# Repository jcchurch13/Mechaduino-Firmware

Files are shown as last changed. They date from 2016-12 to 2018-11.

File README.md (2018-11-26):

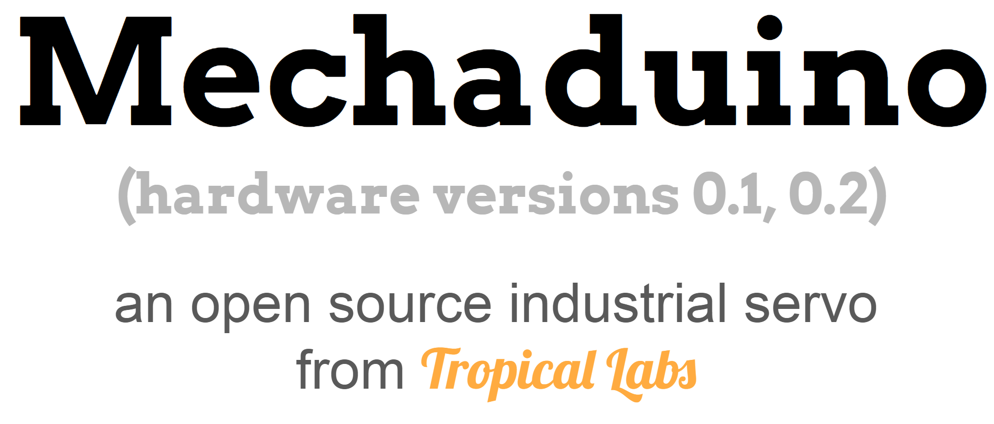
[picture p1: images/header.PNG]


New release 11/26/2018!  The calibration table is now stored in flash memory!  (Many thanks to osresearch!) We've also fixed a couple of small bugs.
Here are some preliminary instructions on how to get your Mechaduino up and running.  For more details, see the Mechaduino Manual above!



## Bootloader:
You will need to make sure your Mechaduino has the latest Arduino Zero bootloader.  If you got your Mechaduino from Tropical Labs, it will already have this! Otherwise you will need an Atmel-ICE or similar SWD programmer...

## Firmware:

Compile the Mechaduino firmware in the Arduino IDE and upload to your Mechaduino.  (Mechaduino will appear as an Arduino Zero.)  

New firmware is in the default "master" branch. Older versions are available [here](https://github.com/jcchurch13/Mechaduino-Firmware/releases). 

## Calibration Routine:

The first thing you will need to do is run the encoder calibration routine.

With the Mechaduino connected to your computer, open a serial monitor (115200 baud) in the Arduino IDE.  You will need to provide V+ to the Mechaduino to power the motor drivers (needed to calibrate).  A menu should appear explaining the basic commands (you can call the menu up at any time by typing 'm').  Type "s" and press enter a couple times to verify that everything is working.  The Mechaduino should step like a stepper.  It is currently in open loop mode.  press "d" and the stepping direction will change.  

Now, make sure nothing will touch the Mechaduino’s shaft during the calibration routine. If possible, completely disconnect any load that is attached to the Mechaduino’s shaft.  Type "c" to start the calibration routine. The Mechaduino will now step through all full steps to calibrate the encoder. In the latest version of the firmware, the calibration table will automatically be stored in non-volatile flash memory. When this routine is complete, your Mechaduino is now calibrated!

## Basic Commands:

As long as you have "serialCheck();" in your main loop, you can use the following built in commands to control the mechaduino from a serial monitor:

s - step (steps one full step in open loop mode)

d - dir (changes step direction in open loop mode)

p - print angle [step count] , [assumed angle] , [encoder reading]

c - calibration routine

e - check encoder diagnostics

q - parameter query (prints current PID values and cal table)

x  -  position mode

v - velocity mode

t - torque mode

y - enable control loop (enter closed loop mode)

n - disable control loop (go back to open loop mode)

r - enter new setpoint (new setpoint for control loop)

j - step response

k - edit controller gains*

g - generate sine commutation table

m - print main menu

  ...see serialCheck() in Utils for more details

##License

All Mechaduino related materials are released under the
[Creative Commons Attribution Share-Alike 4.0 License](https://creativecommons.org/licenses/by-sa/4.0/)

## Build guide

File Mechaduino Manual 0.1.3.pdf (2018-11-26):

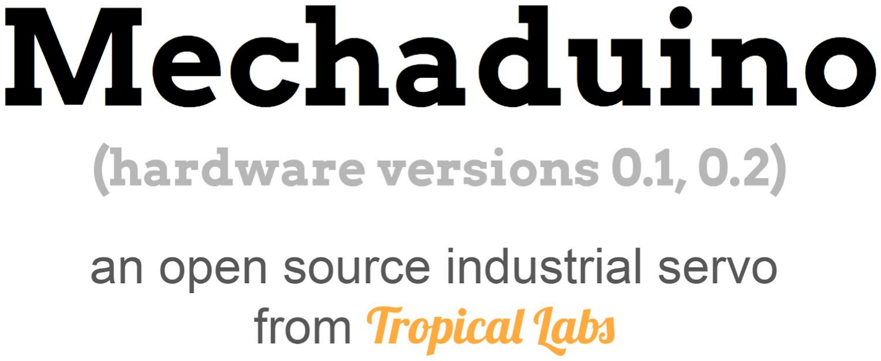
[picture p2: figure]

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
al v

0.1.3

# Table of Contents

Table of Contents | 2
Introduction | 4
Updates | 5
Overview of Specifications | 6
Microcontroller: SAMD21G18A | 6
Encoder: AS5047D or AS5048A | 6
Motor Driver: A4954 | 6
Motor included with Mechaduino Servo: 17HS16-2004S1 | 6
Magnet: Diametrically Magnetized NdFeBr | 7
Mounting Hardware: | 7
Getting Started | 8
Assembly: | 8
Firmware: | 9
Calibration Routine: | 10
Basic Commands: | 11
First Moves: | 12
Troubleshooting | 13
Tune Control Loop: | 14
Hardware: | 15
Board Versions: | 15
Board Layout | 16
Pin Diagram | 17
Power Connections | 18
Step/Dir Wiring Diagram | 19
Firmware v0.1.5 | 20
Overview | 20
Files | 20
Block Diagram | 21
Variables | 21
Control Algorithms: | 22
Position Mode: | 22

Mechaduino Manual v0.1.3

Velocity Mode: | 23
Torque Mode: | 23
Functions | 24
Examples | 25
Serial Interface | 25
Step/Dir Interface | 26
Button | 28
Print | 29
Torque Detect | 30
Slow Moves | 31
License | 33

# Introduction

Mechaduino is an Arduino for mechatronics! Mechaduino is a self-contained motion control platform which allows you to develop your own custom servo mechanisms. It can be also be used as a drop-in servo motor for 3D printers and CNC machines. No more missed steps!

# Updates

There are a few updates to the Mechaduino firmware in version v0.1.5:

- Calibration routine is now automatically stored in nonvolatile flash memory!
- Setpoint is set to current position when closed loop is enabled.
- Phase currents are set to zero (off) when closed loop is disabled.

In this version of the Mechaduino Manual, we’ve added documentation for the new calibration routine. We’ve also added in some notes and clarifications to address frequently asked questions.

# Overview of Specifications

Microcontroller: SAMD21G18A (http://www.atmel.com/Images/Atmel-42181-SAM-D21_Datasheet.pdf)

ARM Cortex-M0+ CPU running at 48MHz
Arduino Zero (https://www.arduino.cc/en/Main/ArduinoBoardZero) compatible
Operating Voltage: 3.3V
NOTE: only pins D0 and D1 have level converters for use with 5V logic. All others are 3.3V
Encoder: | AS5047D (http://www.mouser.com/ds/2/588/AS5047D_DS000394_2-00-347336.pdf) or AS5048A (https://www.mouser.com/datasheet/2/588/AS5048_DS000298_4-00-1100510.pdf)

^ (March-June 2018 - see note)
Resolution: | 14bit
Accuracy: | about ±0.1° worst case after calibration routine*
Interface: | SPI
Motor Driver: | A4954 (http://www.allegromicro.com/~/media/Files/Datasheets/A4954-Datasheet.ashx)

Dual Full-Bridge DMOS PWM Motor Driver
Peak output currents: ±2 A

Motor included with Mechaduino Servo: 17HS16-2004S1 (https://www.omc-stepperonline.com/hybrid-stepper-motor/nema-17-bipolar-45ncm-64ozin-2a-42x40mm-4wires-w-1m-cable-and-connector-17hs16-2004s1.html)

Motor Type: | Bipolar Stepper
Step angle: | 1.8°
Holding Torque: | 45Ncm (63.7oz.in)
Rated Current/phase: | 2A
Phases: | 2
Positional accuracy: | ±5%
Phase Resistance: | 1.1ohms
Inductance: | 2.6mH±20%(1KHz)
Rotor Inertia | 54gcm²
Frame Size: | NEMA 17 (42mm X42mm)

*This is limited by the positional accuracy of the stepper motor that you use. This encoder has an integral nonlinearity of up to ±0.8°. Our calibration routine uses the stepper motor’s full step positions as references to calibrate out most of this error. Most stepper motors claim a full step accuracy of ±5% or better.

Magnet: Diametrically Magnetized NdFeBr (http://www.kjmagnetics.com/proddetail.asp?prod=D42DIA)

Mount about 1mm-2mm from encoder chip. Use epoxy/superglue to secure to shaft. Calibration routine corrects for minor misalignment.

## Mounting Hardware:

We use m3 threaded rods epoxied into 4mm M3 standoffs. Be careful not to remove all motor screws at once while installing: Opening a stepper motor can weaken its magnetization.

# Getting Started

### Assembly:

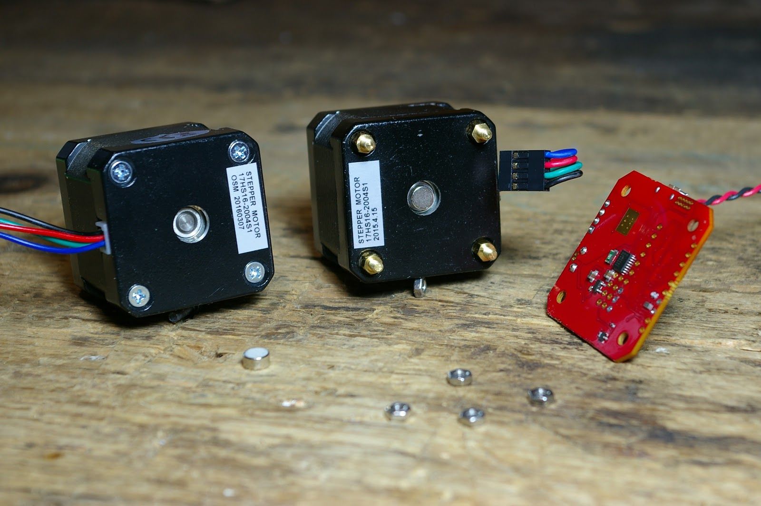
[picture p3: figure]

You will need to mount the magnet to the back of the motor shaft. Note: the magnet must be diametrically magnetized, as opposed to axially magnetized. The magnet may naturally stick to the shaft, but we recommend a dab of epoxy or super glue to hold it in place. The magnet should be fairly centered, but the calibration routine will correct for minor misalignment.

The Mechaduino PCB must be mounted so that the magnet is directly under the encoder chip. (Close but not touching. About 1-2mm. See the AS5047/AS5048 datasheet for details.) We replaced the standard motor hardware with M3 threaded rods and short standoffs to mount on our assembled Mechaduino Servos, but there are other ways this could be done.

When wiring your motor up to the Mechaduino board, please make sure that one phase is connected to outputs 1&2, and the other phase is connected to outputs 3&4.

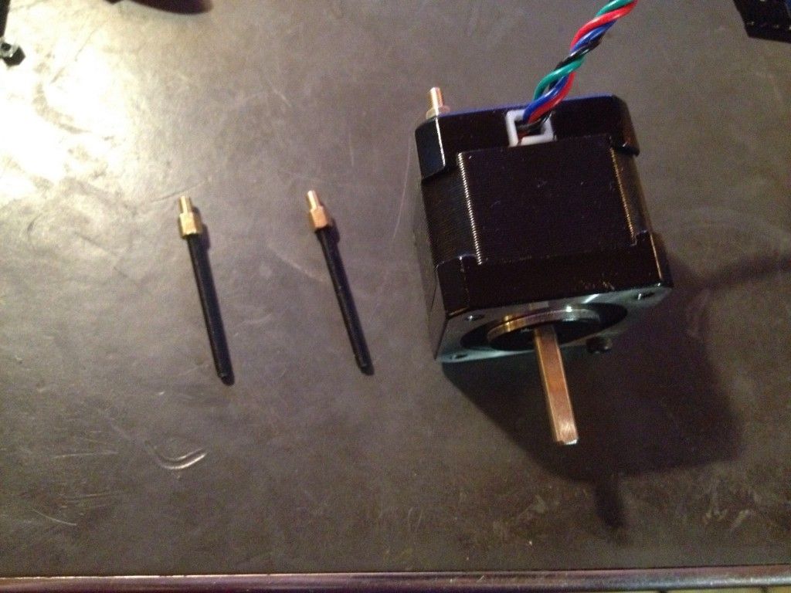
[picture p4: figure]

## Firmware:

Next, you need to install the firmware:

The Mechaduino firmware can be compiled/edited/uploaded using the popular Arduino IDE:

https://www.arduino.cc/en/Main/Software

Once you have the Arduino IDE installed, you will need to add Arduino Zero support. Open the Arduino IDE, navigate to Tools>Board:...>Board Manager and install the latest "Arduino SAMD (32-bits ARM Cortex-M0+)" .

Now go to Tools>Board and select “Arduino/Genuino Zero (Native USB Port)”.

At this point you can connect your Mechaduino via USB. It will appear as an Arduino Zero. (If it does not appear, please make sure any drivers have finished installing, then try hitting the reset button or disconnecting/reconnecting the hardware. Double clicking the reset button puts the arduino zero into a “bootloader mode” which may make it easier to connect to.)

Download the latest Mechaduino firmware (https://github.com/jcchurch13/Mechaduino-Firmware) (the ‘master’ branch on GitHub), open it in the Arduino IDE, compile it, and upload to your Mechaduino. Previous versions of the firmware are available here. (https://github.com/jcchurch13/Mechaduino-Firmware/releases)

### 1.8 vs 0.9 degree steppers:

By default the firmware assumes a 1.8 degree (200 steps per rev) stepper. If you are using a 0.9 degree (400 steps per rev) or other size stepper, you will need to adjust the parameter “spr” (steps per rev) in parameters.cpp.

const int spr = 200; // 200 steps per revolution -- for 400 step/rev, you only need to edit this value

## Calibration Routine:

Once you have the firmware installed, you will need to run the encoder calibration routine.

With the Mechaduino connected to your computer, open a serial monitor (115200 baud) in the Arduino IDE. You will need to provide V+ to the Mechaduino to power the motor drivers (needed to calibrate). Type "s" and press enter a couple times to verify that everything is working. The Mechaduino should step like a stepper. It is currently in open loop mode. press "d" and the stepping direction will change.

Now, make sure nothing will touch the Mechaduino’s shaft during the calibration routine. If possible, completely disconnect any load that is attached to the Mechaduino’s shaft. Type "c" to start the calibration routine. The Mechaduino will now step through all full steps to calibrate the encoder. In the latest version of the firmware, the calibration table will automatically be stored in non-volatile flash memory. When this routine is complete, your Mechaduino is now calibrated!

Please note that the calibration table will be overwritten if you re-upload the firmware. While it is no longer necessary to copy a lookup table into the firmware to complete the calibration, you may want to do so in order to avoid having to recalibrate. You can print the calibration table to the serial monitor by pressing “q”. A very long lookup table (16,384 entries) will be printed to the serial monitor. These are the calibrated angles at each encoder count. You can copy these into the Parameters.cpp file here:

//This is the encoder lookup table (created by calibration routine):

const float __attribute__((__aligned__(256))) lookup[16384] = { //Put lookup table here!
};

You can easily select the whole lookup table from the serial monitor by clicking on the next line and dragging the cursor up.
Save, compile, and re-upload the firmware to your Mechaduino. Your Mechaduino is now ready to use without re-calibrating. Please note that you will need to generate a new calibration table for each Mechaduino.

## Basic Commands:

As long as you have "serialCheck();" in your main loop, you can use the following built in commands to control the Mechaduino from a serial monitor:

Implemented serial commands are:

s - step | (steps one full step in open loop mode)
d - dir | (changes step direction in open loop mode)
p - print angle [step count] , [assumed angle] , [encoder reading]

c - calibration routine
e - check encoder diagnostics (does not work in closed loop mode)
q - parameter query | (prints current PID values and cal table)
x - position mode | (set mode for closed loop operation)
v - velocity mode
t - torque mode
y - enable control loop | (enter closed loop mode)
n - disable control loop | (go back to open loop mode)
r - enter new setpoint | (new setpoint for control loop)

j - step response
k - edit controller gains*
g - generate sine commutation table m - print main menu

See serialCheck() in Utils for more details

*Note, these edits are stored in volatile memory and will be reset if power is cycled

## First Moves:

Once you’ve calibrated the Mechaduino, try out the closed loop position mode:

1. Type “x” and then enter into the serial monitor to set position mode.
2. Type “y” then enter to enable closed loop mode.
3. Type “r” and then enter to change the setpoint. You will be prompted to enter a setpoint angle.
4. Try entering various setpoint to see how the mechaduino moves. For example, try 0 to find where zero is, and then try 720 to see the Mechaduino do two full rotations. Try 0 and then 0.5 to see the Mechaduino move half of a degree.
5. Try moving the Mechaduino’s shaft with your hand. Watch to make sure it returns to the desired setpoint.
6. Disable closed loop mode by typing “n” and then enter.

Set the setpoint back to zero, and then try out velocity and torque modes in the same way as above. (Make sure the setpoint is zero before changing modes to avoid rapid movements!)

## Troubleshooting:

If you are having trouble connecting and uploading to the Mechaduino, please try the following:

- Make sure you have “Arduino/Genuino Zero (Native USB Port)” selected under Tools>Board in the Arduino IDE.
- Try clicking/double clicking the reset button on the Mechaduino.

If neither of those work, please check to make sure that the Mechaduino is appearing as a COM port under Tools>Com. The port number may change if you disconnect the Mechaduino, hit reset, or upload firmware. If it does not appear at all, there may be an issue with your hardware.

If closed loop mode does not behave as expected:

- First, try running in closed loop mode without a mechanical load, using the default controller parameters. Depending on the load, you may need to tune the controller.
- Make sure your lookup table looks reasonable. You can view the lookup table by pressing ‘q’ in the serial monitor. You should see ascending values that increment by approximately 0.02 per entry, wrapping around to zero once they reach 360.
- If the lookup table does not look right, make sure the magnet is placed close enough to the encoder on the Mechaduino. Try the ‘e’ command to view the encoder diagnostics (do this in open loop mode. Readings may be erratic in closed loop mode).

## Tune Control Loop:

At this point you may need to tune the controller gains. By default, the position and velocity loops have PID controllers with parameters that can be edited in Parameters.cpp:

//----Current Parameters-----

volatile float Fs = 6500.0; | //Sample frequency in Hz
volatile float pKp = 10.0; | //position mode PID values.
volatile float pKi = 0.15;
volatile float pKd = 20.0;
volatile float vKp = 0.05; | //velocity mode PID values.
volatile float vKi = 0.033;
volatile float vKd = 3.0;

To tune the control loop from the serial monitor:
- Connect your Mechaduino to your computer and open up a serial monitor
- Use the commands ‘x’ followed by ‘y’ to enter closed loop position mode
- Use the command ‘k’ to bring up the tuning menu
- Adjust the parameters until you get a good response
- To make these changes permanent, you will need to copy these values into the Parameters.cpp file and re-upload.
- You can compare tunings by using the step response command ‘j’. (You must exit the tuning menu first.)

PID values will vary a lot depending on the motor you use and the load you have connected to your motor. There are lots of resources online that discuss PID tuning, but here are some simple pointers:
-Start with a low proportional gain and no integral or derivative action. If the motor seems to buzz or behave erratically, then your Kp is probably too high. Try setting Kp low enough that the motor behaves like a fairly compliant spring about the setpoint.
-Slowly increase Kp to improve the stiffness of the control. Adding integral action can remove steady state errors. Derivative action can also be added in to improve performance.

# Hardware:

## Board Versions:

The Mechaduino 0.2 hardware is backwards compatible with the Mechaduino 0.1 and features the following improvements:

- Four 5V level-shifted digital I/O (D0, D1, D2, & D3)
- Better thermal design for A4954 driver
- Higher voltage capacitors allow for a max V+ of 35V
- Small vias provided to break out encoder A/B/I interface and rsense voltages (for experimental use)
- No more traces under mounting screws*
- No traces under AS5047 encoder
- Simplified power circuit

Note: Mechaduinos purchased between 3/1/2018 amd 7/1/2018 used an AS5048A encoder instead of the AS5047D (due to supply availability). As far as the Mechaduino is concerned, the two parts are virtually identical. However, we just became aware that the as5048a's error register has a slightly different address. To correct this issue, you can change lines 610 and 611 in Utils.cpp to the following:

SPI.transfer(0x7F);
SPI.transfer(0xFD);

*Bottom solder mask under OSHW logo can be scraped away to provide single ground point to motor.

## Board Layout

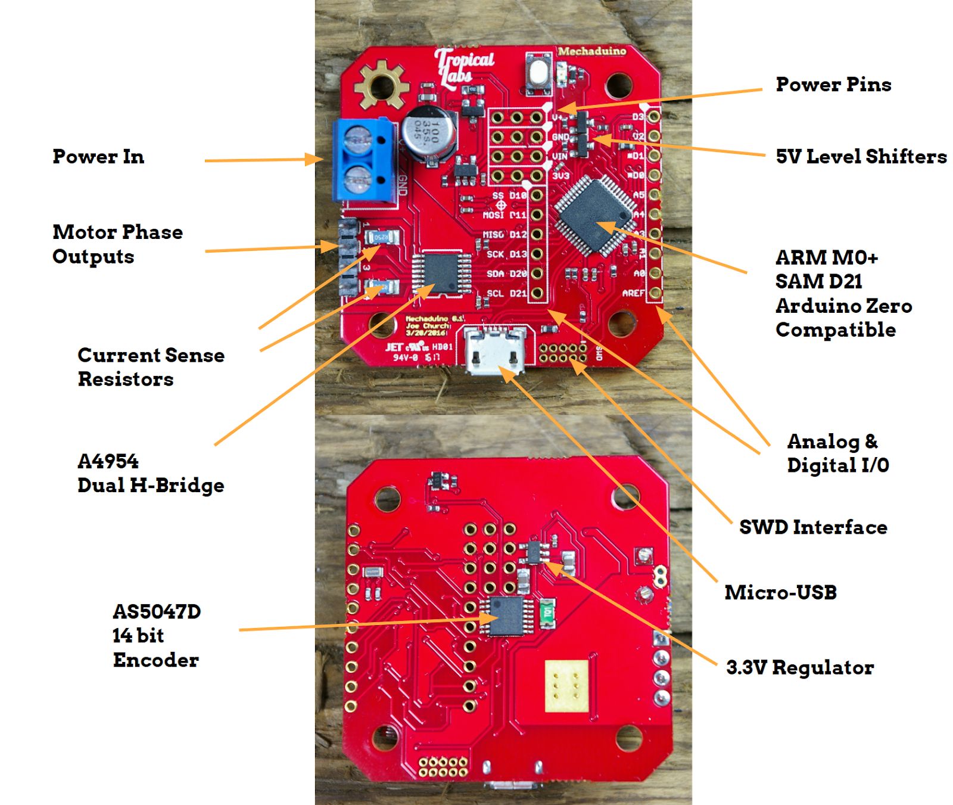
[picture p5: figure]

Version 0.1 shown, version 0.2 is very similar.

## Pin Diagram

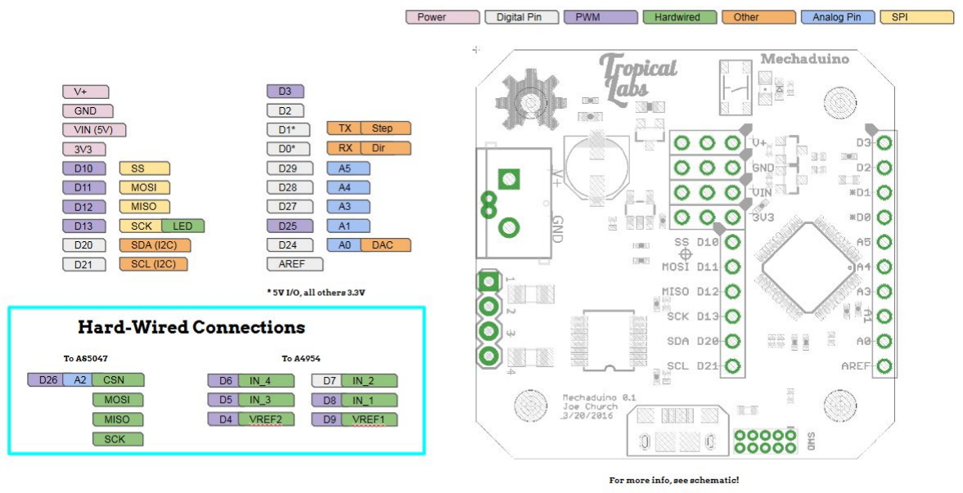
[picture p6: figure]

Version 0.1 shown, version 0.2 has four 5V I/O : D0,D1,D2,& D3.

## Power Connections

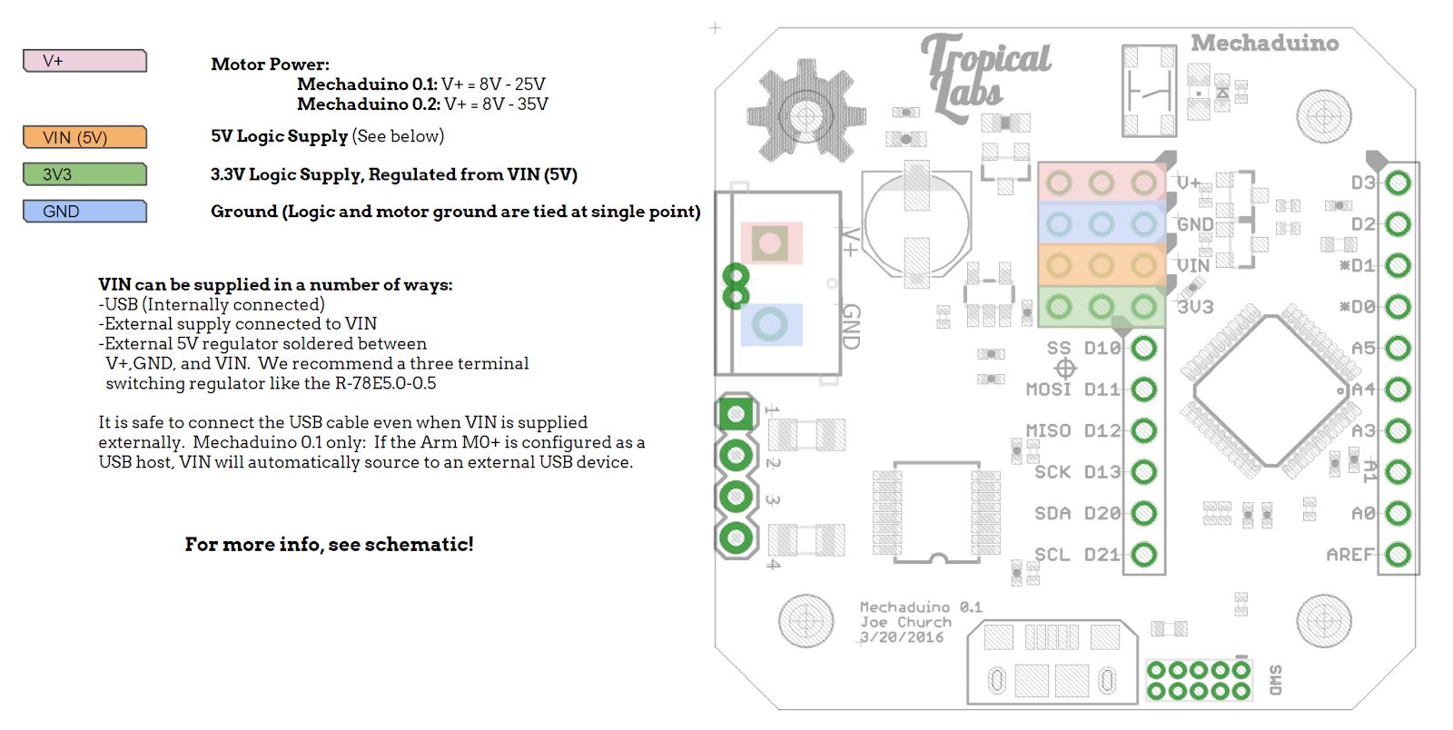
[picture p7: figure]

## Step/Dir Wiring Diagram

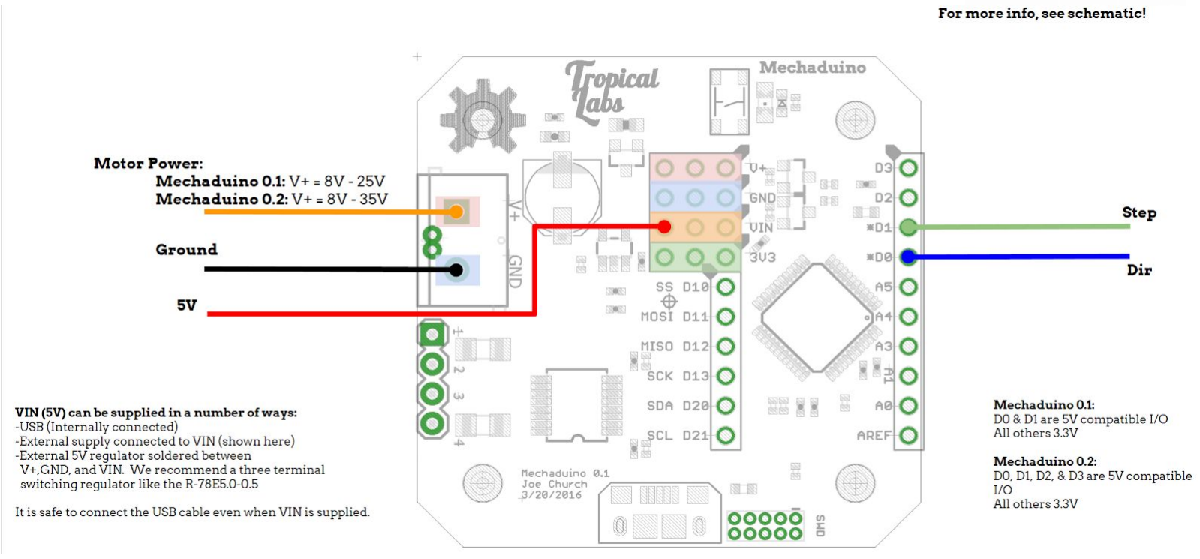
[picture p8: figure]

# Firmware v0.1.5

## Overview

The Mechaduino Firmware can be edited, compiled and uploaded from the popular Arduino IDE. It is written in Arduino language (https://www.arduino.cc/en/Reference/HomePage) (similar to C/C++). You can script the Mechaduino’s behavior in the main loop of the file Mechaduino_01.ino. The stock Mechaduino firmware is configured to listen for serial commands using serialCheck(). A step/dir interrupt can be enabled to increment/decrement the setpoint variable.

## Files

Mechaduino_01.ino
This is the main file that contains setup(), (https://www.arduino.cc/en/Reference/Setup) which runs once on startup and loop() (https://www.arduino.cc/en/Reference/Loop) which runs thereafter.

Controller.cpp
Contains the TC5_Handler() which executes at 6.5kHz* when enabled and contains the closed loop control algorithms. For more info on configuring TC5, please see this. (http://www.atmel.com/Images/Atmel-42181-SAM-D21_Datasheet.pdf#page=635)

Parameters.cpp
Contains configurable parameters including PID gains, calibration table, and other constants.

State.cpp
Contains controller state variables.

Utils.cpp
Contains utility function definitions.

AnalogFastWrite.c
The latest arduino zero board files (1.6.7 and up) have a much lower PWM frequency than previous versions (732.4Hz , down from 187.5kHz). This causes audible hissing when used with the Mechaduino. We added the
analogFastWrite command to provide 187.5kHz PWM to eliminate this issue.

Additionally, the header files (.h) contain function declarations and macro definitions for the above files. Utils.h is a good reference since it gives a list of all the implemented utility functions.

*Set by Fs in Parameters.cpp which changes TC5->COUNT16.CC[0].reg = (int)( round(48000000 / Fs)); in setupTCInterrupts() in Utils.cpp.

## Block Diagram

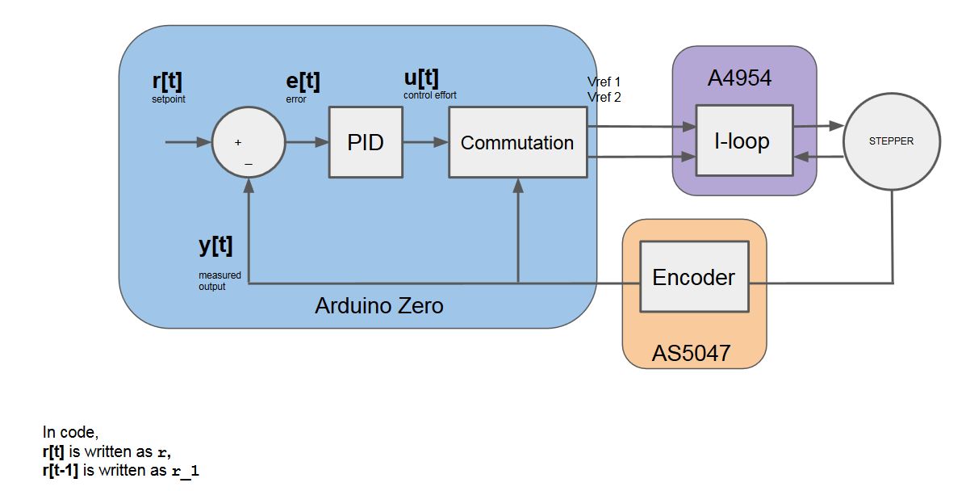
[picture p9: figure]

## Variables

Important global variables include controller state variables and configuration parameters. While the use of global variables is sometimes frowned upon, we wanted these values to be accessible and modifiable to make it easier to develop custom applications (see the example section of this document). Similarly, we chose to use floating point math for the controller instead of fixed point math. While fixed point math would be faster, we’ve found that our floating point algorithms are generally fast enough, and are much more readable. As a result, many of these variables are floats. Here is an overview:

Name | Description | Type | range | unit | Definition Location
r | Control loop setpoint | float | N/A | Degrees in position mode…. | State.cpp
y | Corrected encoder reading | float | 0.0 to 360.0 | degrees | State.cpp
yw | Wrapped angle (keeps track of revolutions) | float | N/A | degrees | State.cpp
e | Error (r-yw) | float | N/A | degrees | State.cpp
u | Control effort | float | -uMAX to uMAX | Bits ( 8.6mA/bit)* | State.cpp

*(3.3V/255bits)*(1A/10*rsense)= 8.6mA

## Control Algorithms:

## Position Mode:

The default position mode controller is a PID controller of the following form (represented as discrete transfer functions (https://en.wikipedia.org/wiki/Transfer_function) using the z-transform): (https://en.wikipedia.org/wiki/Z-transform)

u(z) = Pterm(z) + Iterm(z) + Dterm(z)

e = r − yw

(z) pKp e

Pterm =

(z)
e

Iterm = z − 1

pKi z

(z) − Kd 1 )
yw
Dterm | = p | * ( − a (z−a) (z−1)

In code, this is implemented with the following difference equations:

e = (r - yw);

ITerm += (pKi * e); | //Integral wind up limit
if (ITerm > 150.0) ITerm = 150.0;
else if (ITerm < -150.0) ITerm = -150.0;

DTerm = pLPFa*DTerm - pLPFb*pKd*(yw-yw_1);

u = (pKp * e) + ITerm + DTerm;

A couple notes:

-Dterm is calculated from angle measurement, yw, rather than from error. This is a common practice that prevents jumps from step reference commands, but provides the same damping. (This is why there is a negative sign: e = r - y)

-Dterm has a first order low pass filter. The breakpoint of the filter is set by adjusting pLPF (in hertz) and is calculated as follows:

a = e

(sTs) = e

(−pLPF*2pi*Ts)
(in code, a is pLPFa)

## Velocity Mode:

The default velocity mode controller is a PID controller of the following form (represented as discrete transfer functions (https://en.wikipedia.org/wiki/Transfer_function) using the z-transform): (https://en.wikipedia.org/wiki/Z-transform)

u(z) = Pterm(z) + Iterm(z) + Dterm(z)

− 1 | ) Fs | 0.16666667

v

yw = ( − a * | * | * (z−a) (z−1)

e = (r − v);

(z) pKp e

Pterm =

(z)
e

Iterm = z − 1 pKi z

(z) Kd e
Dterm | = p | * (z) (z−1)

In code, this is implemented with the following difference equations:

v = -(vLPFa*v + vLPFb*(yw-yw_1)); | //filtered velocity
e = (r + v); | //error in degrees per rpm (sample frequency in Hz*(60 seconds/min)/(360 degrees/rev))
ITerm += (vKi * e); | //Integral wind up limit
if (ITerm > 200) ITerm = 200;
else if (ITerm < -200) ITerm = -200;

u = ((vKp * e) + ITerm - (vKd * (e-e_1)));

A couple notes:

v, the filtered, measured velocity, has a first order low pass filter. The breakpoint of the filter is set by adjusting pLPF (in hertz) and is calculated as follows:

a = e

(sTs) = e

(−pLPF*2pi*Ts)
(in code, a is vLPFa)

## Torque Mode:

In torque mode, the setpoint r directly sets the control effort u, which in turn sets the current level. The a4954 driver chip has an internal current loop that forces the motor phase current to the commanded level. The torque exerted by the Mechaduino is equal to the motor torque constant times the phase current.

## Functions

void setupPins(); | // initializes pins
void setupSPI(); | // initializes SPI
void configureStepDir(); | // configure step/dir interface
void configureEnablePin(); | // configure enable pin
void stepInterrupt(); | // step interrupt handler
void dirInterrupt(); | // dir interrupt handler
void enableInterrupt(); | // enable pin interrupt handler
void output(float theta, int effort); | // calculates phase currents (commutation) and outputs to Vref pins
void calibrate(); | // calibration routine
void serialCheck(); | // checks serial port for commands. Must include this in loop() for serial interface to work
void parameterQuery(); | // prints current parameters
void oneStep(void); | // take one step
int readEncoder(); | // read raw encoder position
void readEncoderDiagnostics(); | // check encoder diagnostics registers
void print_angle(); | // for debugging purposes in open loop mode: prints [step number] , [encoder reading]
void receiveEvent(int howMany); | // for i2c interface...
int mod(int xMod, int mMod); | // modulo, handles negative values properly
void setupTCInterrupts(); | // configures control loop interrupt
void enableTCInterrupts(); | // enables control loop interrupt. Use this to enable "closed-loop" modes
void disableTCInterrupts(); | // disables control loop interrupt. Use this to disable "closed-loop" mode
void antiCoggingCal(); | // under development...
void parameterEditmain(); | // parameter editing menu
void parameterEditp(); | // parameter editing menu
void parameterEditv(); | // parameter editing menu
void parameterEdito(); | // parameter editing menu
void hybridControl(); | // open loop stepping, but corrects for missed steps. under development
void serialMenu(); | // main menu
void sineGen(); | // generates sinusoidal commutation table. you can experiment with other commutation profiles
void stepResponse(); | // generates position mode step response in Serial Plotter
void moveRel(float pos_final,int vel_max, int accel); | // Generates trapezoidal motion profile for closed loop position mode
void moveAbs(float pos_final,int vel_max, int accel); | // Generates trapezoidal motion profile for closed loop position mode

# Examples

Below are a few examples. Please note that there are a few changes from previous versions of the firmware (specifically for the step/dir interface).

## Serial Interface

As long as the function serialCheck() is included in your loop (it is by default), you can use the built in serial commands. (Full list here.) You can also create your own by creating a function and adding it to serialCheck().

The serial interface is useful for debugging/initial testing. Generally, when using a Mechaduino in a new application, we might do the following:

- Connect to computer, open serial monitor
- Run cal routine, copy table to firmware, recompile, and upload
- Connect Mechaduino to mechanical load
- Set closed loop position mode using commands ‘x’, ‘y’
- Tune PID loop using ‘k’ (parameter edit) and ‘j’ (step response) commands
- Copy best PID values to firmware, recompile, and upload
- Move Mechaduino to various setpoints in closed loop mode using ‘r’ command to test out application

## Step/Dir Interface

Here is how to correctly enable the step/dir interface for use with a 3D printer/CNC machine after calibrating and tuning your PID loop.

void setup() | // This code runs once at startup
{
digitalWrite(ledPin,HIGH); | // turn LED on
setupPins(); | // configure pins
setupTCInterrupts(); | // configure controller interrupt

SerialUSB.begin(115200);
delay(3000); | // This delay seems to make it easier to establish a connection when the
Mechaduino is configured to start in closed loop mode.
serialMenu(); | // Prints menu to serial monitor
setupSPI(); | // Sets up SPI for communicating with encoder
digitalWrite(ledPin,LOW); | // turn LED off

// Uncomment the below lines as needed for your application.
// Leave commented for initial calibration and tuning.
| configureStepDir(); | // Configures setpoint to be controlled by step/dir interface
// | configureEnablePin(); | // Active low, for use wath RAMPS 1.4 or similar
| enableTCInterrupts(); | // uncomment this line to start in closed loop
| mode = 'x'; | // start in position mode
}

////////////////////////////////////// /////////////////LOOP///////////////// //////////////////////////////////////

void loop() | // main loop
{
serialCheck(); | //must have this execute in loop for serial commands to function
//r=0.1125*step_count; | //Don't use this anymore, step interrupts enabled above by //"configureStepDir()", adjust step size in parameters.cpp

}

You can adjust the step size by changing the stepangle variable in Parameters.cpp:

const int spr = 200; // 200 steps per revolution -- for 400 step/rev, you only need to edit this value
const float aps = 360.0/ spr; | // angle per step
int cpr = 16384; | // counts per rev
const float stepangle = aps/32.0; | // for step/dir interrupt: aps/32 is the equivalent of 1/32 microsteps

By default the stepangle is set to the equivalent of 1/32 microstepping.

If you would like to use an enable pin, you can uncomment this line:

configureEnablePin(); | // Active low, for use wath RAMPS 1.4 or similar

Note that only pins D0 & D1 have built in level converters. You will need to step down a 5V enable signal to 3.3V. You could use a level converter board like this, (https://www.sparkfun.com/products/12009) or a simple resistor divider.

## Button

In this code, when digital pin 3 goes HIGH, the Mechaduino moves from 0 to 90 degrees, holds that position for 3 seconds, and then goes back.

void setup() | // This code runs once at startup
{
digitalWrite(ledPin,HIGH); | // turn LED on
setupPins(); | // configure pins
setupTCInterrupts(); | // configure controller interrupt

SerialUSB.begin(115200);
delay(3000); | // This delay seems to make it easier to establish a connection when the
Mechaduino is configured to start in closed loop mode.
serialMenu(); | // Prints menu to serial monitor
setupSPI(); | // Sets up SPI for communicating with encoder
digitalWrite(ledPin,LOW); | // turn LED off

// Uncomment the below lines as needed for your application.
// Leave commented for initial calibration and tuning.
// | configureStepDir(); | // Configures setpoint to be controlled by step/dir interface
// | configureEnablePin(); | // Active low, for use wath RAMPS 1.4 or similar
| enableTCInterrupts(); | // uncomment this line to start in closed loop
| mode = 'x'; | // start in position mode

pinMode(3, INPUT);
}

////////////////////////////////////// /////////////////LOOP///////////////// //////////////////////////////////////

void loop() | // main loop
{
r = 0;
if (digitalRead(3) == HIGH){
r = 90;
delay(3000);
}
}

## Print

Here is some demo code showing how to print some of the the state variables to the serial monitor while the Mechaduino is running. You can access these variables and use them in other ways as well. For example you could toggle some of the GPIO depending on the value of the position error e, or you could set an analog out pin proportional to the control effort u.

void setup() | // This code runs once at startup
{
digitalWrite(ledPin,HIGH); | // turn LED on
setupPins(); | // configure pins
setupTCInterrupts(); | // configure controller interrupt

SerialUSB.begin(115200);
delay(3000); | // This delay seems to make it easier to establish a connection when the
Mechaduino is configured to start in closed loop mode.
serialMenu(); | // Prints menu to serial monitor
setupSPI(); | // Sets up SPI for communicating with encoder
digitalWrite(ledPin,LOW); | // turn LED off

// Uncomment the below lines as needed for your application.
// Leave commented for initial calibration and tuning.
// | configureStepDir(); | // Configures setpoint to be controlled by step/dir interface
// | configureEnablePin(); | // Active low, for use wath RAMPS 1.4 or similar
| enableTCInterrupts(); | // uncomment this line to start in closed loop
| mode = 'x'; | // start in position mode

}

////////////////////////////////////// /////////////////LOOP///////////////// //////////////////////////////////////

void loop() | // main loop
{
serialCheck();

SerialUSB.print("setpoint: "); SerialUSB.print(r);
SerialUSB.print(", error: "); SerialUSB.println(e);
delay(100); //delay 0.1 seconds }

## Torque Detect

The Mechaduino can detect and react to external disturbances. In this example, exerting a slight torque in either direction on the Mechaduino’s rotor will cause the setpoint to advance in the corresponding direction by 90 degrees:

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

}

////////////////////////////////////// /////////////////LOOP///////////////// //////////////////////////////////////

void loop() | // main loop
{
if (u > 35){
r -= 90;
delay(100);
}
else if (u < -35){
r += 90;
delay(100);
}
}

The torque is detected by monitoring the control effort u in closed loop position mode.

## Slow Moves

By design, setting a setpoint in position mode causes the Mechaduino to snap to the new setpoint as fast as possible. This is not always ideal. There are a number of ways to create slow smooth motion in position mode.

One way is to use an external motion controller to create a trajectory of setpoints for the Mechaduino to follow. An example of this would be using the Mechaduino’s step/dir interface with a 3D printer or CNC machine. Here the motion profiles are generated in external firmware/software such as Marlin or Mach 3.

If you would like smooth motion in a stand-alone application, you can generate your motion profile on the Mechaduino itself. To illustrate this, here is a crude loop that will move the Mechaduinos setpoint from 0 to 90 degrees and back at constant speed:

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

SerialUSB.begin(115200);
delay(3000);
serialMenu(); | // Prints menu to serial monitor
setupSPI(); | // Sets up SPI for communicating with encoder
digitalWrite(ledPin,LOW); | // turn LED off

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

//////////////////////////////////////
/////////////////LOOP///////////////// //////////////////////////////////////
void loop() | // main loop
{

while (r < 90.0){
r += 0.1;
delayMicroseconds(100);
}
delay(2000);
while (r > 0.0){
r -= 0.1;
delayMicroseconds(100);
}
delay(2000);
}

We’ve gone a step further and implemented two commands that generate trapezoidal speed trajectories (constant acceleration, max speed, constant deceleration): moveRel() for relative movements; and moveAbs() for absolute movements. From Parameters.cpp:

void moveAbs(float pos_final,int vel_max, int accel){

//Use this function for slow absolute movements in closed loop position mode
//
// This function creates a "trapezoidal speed" trajectory (constant accel, and max speed, constant decel); // It works pretty well, but it may not be perfect
//
// pos_final is the desired position in degrees
// vel_max is the max velocity in degrees/second
// accel is the max accel in degrees/second^2
//
//Note that the actual max velocity is limited by the execution speed of all the math below. //Adjusting dpos (delta position, or step size) allows you to trade higher speeds for smoother motion //Max speed with dpos = 0.225 degrees is about 180 deg/sec
//Max speed with dpos = 0.45 degrees is about 360 deg/sec

And here’s an example showing how to use these functions:

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

SerialUSB.begin(115200);
delay(3000);
serialMenu(); | // Prints menu to serial monitor
setupSPI(); | // Sets up SPI for communicating with encoder
digitalWrite(ledPin,LOW); | // turn LED off

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

//////////////////////////////////////
/////////////////LOOP///////////////// //////////////////////////////////////
void loop() | // main loop
{
moveRel(360.0,100, 30);
delay(2000);
moveAbs(0.0,100,30);
delay(2000);
}

# License

All Mechaduino related materials are released under the Creative Commons Attribution Share-Alike 4.0 License (https://creativecommons.org/licenses/by-sa/4.0/)

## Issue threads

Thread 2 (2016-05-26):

Effective CPR count

iceblu3710, 2016-05-26:
From the code `int cpr = 16384; //counts per rev` seems quite an achievement with a hall effect encoder. What is the effective CPR that can be independently held and stepped to/from reliably?

jcchurch13, 2016-05-29:
Thanks for taking a look at our code!

CPR is our encoder "Counts Per Revolution": 2^14 or 16384.  Our closed loop position control actively forces the motor to move until the correct encoder position is reached.  This gives a resolution of 360 degrees/ 16384 = 0.02 degrees.  Thanks to our calibration routine, the accuracy should be close to the same (we're going to measure this soon).

We have measured repeatability by stepping into and out of full step positions in open loop mode 1000x and looking at the distribution of encoder readings. The results look promising:  I don't have the data in front of me, but the error distribution appeared to be Gaussian with zero mean, and a standard deviation of less than 1 LSB (0.02) degrees.  I'll post this data soon.

Thanks for your interest!  We're looking to get a really accurate, high resolution encoder for a test jig to measure the Mechaduinos accuracy at all encoder increments, not just one position.

Closed 2016-06-22.

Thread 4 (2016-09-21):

Debugging units: No movement in closed loop

SloMusti, 2016-09-21:
Self-built Mechaduino while waiting for Kickstarter units to arrive. Performed calibration routine and programmed it. Step mode with "s" command works. After sending "y" and "x" and "r 1080" no rotation occurs. Stepper axis can be easily moved my hand, there is some minor resistance, but no closed-loop control action occurs.

What parameters in the firmware to observe or print to evaluate what is going on.

jcchurch13, 2016-09-21:
Sounds like this may be an encoder issue.  Did the calibration routine yield a lookup table with numbers ascending by about 0.02?

SloMusti, 2016-09-22:
Please see the calibration values below, seems quite ok in the way the values are increasing. I have tried with different magnets and motors, but the problem persisted. I doubt the problem is in the H bridge or so as it works fine in the open loop step mode. But as soon as it gets into the closed loop mode, there is almost no torque on the axis.

`60.01 , 60.05 , 60.10 , 60.14 , 60.19 , 60.23 , 60.27 , 60.32 , 60.36 , 60.40 , 60.45 , 60.49 , 60.54 , 60.58 , 60.62 , 60.67 , 60.71 , 60.76 , 60.80 , 60.84 , 60.89 , 60.93 , 60.98 , 61.02 , 61.06 , 61.11 , 61.15 , 61.19 , 61.24 , 61.28 , 61.33 , 61.37 , 61.41 , 61.46 , 61.50 , 61.55 , 61.59 , 61.63 , 61.68 , 61.72 , 61.77 , 61.78 , 61.83 , 61.87 , 61.92 , 61.96 , 62.01 , 62.05 , 62.10 , 62.14 , 62.19 , 62.23 , 62.28 , 62.32 , 62.37 , 62.41 , 62.46 , 62.50 , 62.55 , 62.59 , 62.64 , 62.68 , 62.73 , 62.77 , 62.82 , 62.86 , 62.91 , 62.95 , 63.00 , 63.04 , 63.09 , 63.13 , 63.18 , 63.22 , 63.27 , 63.31 , 63.36 , 63.40 , 63.45 , 63.49 , 63.54 , 63.61 , 63.65 , 63.70 , 63.74 , 63.79 , 63.83 , 63.87 , 63.92 , 63.96 , 64.00 , 64.05 , 64.09 , 64.14 , 64.18 , 64.22 , 64.27 , 64.31 , 64.36 , 64.40 , 64.44 , 64.49 , 64.53 , 64.58 , 64.62 , 64.66 , 64.71 , 64.75 , 64.79 , 64.84 , 64.88 , 64.93 , 64.97 , 65.01 , 65.06 , 65.10 , 65.15 , 65.19 , 65.23 , 65.28 , 65.32 , 65.37 , 65.51 , 65.56 , 65.60 , 65.64 , 65.68 , 65.72 , 65.76 , 65.79 , 65.83 , 65.87 , 65.92 , 65.96 , 66.00 , 66.04 , 66.08 , 66.11 , 66.15 , 66.19 , 66.24 , 66.28 , 66.32 , 66.36 , 66.40 , 66.43 , 66.47 , 66.51 , 66.56 , 66.60 , 66.64 , 66.68 , 66.72 , 66.76 , 66.79 , 66.83 , 66.87 , 66.92 , 66.96 , 67.00 , 67.04 , 67.08 , 67.11 , 67.15 , 67.19 , 67.24 , 67.28 , 67.26 , 67.31 , 67.35 , 67.39 , 67.43 , 67.47 , 67.52 , 67.56 , 67.60 , 67.64 , 67.68 , 67.73 , 67.77 , 67.81 , 67.85 , 67.89 , 67.93 , 67.98 , 68.02 , 68.06 , 68.10 , 68.14 , 68.19 , 68.23 , 68.27 , 68.31 , 68.35 , 68.40 , 68.44 , 68.48 , 68.52 , 68.56 , 68.60 , 68.65 , 68.69 , 68.73 , 68.77 , 68.81 , 68.86 , 68.90 , 68.94 , 68.98 , 69.02 , 68.95 , 69.00 , 69.04 , 69.09 , 69.13 , 69.18 , 69.23 , 69.27 , 69.32 , 69.36 , 69.41 , 69.46 , 69.50 , 69.55 , 69.60 , 69.64 , 69.69 , 69.73 , 69.78 , 69.83 , 69.87 , 69.92 , 69.96 , 70.01 , 70.06 , 70.10 , 70.15 , 70.19 , 70.24 , 70.29 , 70.33 , 70.38 , 70.43 , 70.47 , 70.52 , 70.56 , 70.61 , 70.66 , 70.70 , 70.81 , 70.85 , 70.90 , 70.94 , 70.99 , 71.03 , 71.07 , 71.12 , 71.16 , 71.20 , 71.25 , 71.29 , 71.34 , 71.38 , 71.42 , 71.47 , 71.51 , 71.56 , 71.60 , 71.64 , 71.69 , 71.73 , 71.78 , 71.82 , 71.86 , 71.91 , 71.95 , 72.00 , 72.04 , 72.08 , 72.13 , 72.17 , 72.21 , 72.26 , 72.30 , 72.35 , 72.39 , 72.43 , 72.48 , 72.52 , 72.57 , 72.71 , 72.75 , 72.79 , 72.83 , 72.87 , 72.92 , 72.96 , 72.99 , 73.03 , 73.07 , 73.11 , 73.15 , 73.19 , 73.24 , 73.28 , 73.31 , 73.35 , 73.39 , 73.43 , 73.47 , 73.51 , 73.56 , 73.60 , 73.63 , 73.67 , 73.71 , 73.75 , 73.79 , 73.83 , 73.87 , 73.92 , 73.96 , 73.99 , 74.03 , 74.07 , 74.11 , 74.15 , 74.19 , 74.24 , 74.28 , 74.31 , 74.35 , 74.39 , 74.43 , 74.47 , 74.49 , 74.53 , 74.57 , 74.61 , 74.65 , 74.69 , 74.74 , 74.78 , 74.82 , 74.86 , 74.90 , 74.94 , 74.98 , 75.02 , 75.06 , 75.10 , 75.15 , 75.19 , 75.23 , 75.27 , 75.31 , 75.35 , 75.39 , 75.43 , 75.47 , 75.51 , 75.55 , 75.60 , 75.64 , 75.68 , 75.72 , 75.76 , 75.80 , 75.84 , 75.88 , 75.92 , 75.96 , 76.00 , 76.04 , 76.09 , 76.13 , 76.17 , 76.21 , 76.25 , 76.18 , 76.23 , 76.27 , 76.32 , 76.36 , 76.41 , 76.45 , 76.50 , 76.54 , 76.59 , 76.63 , 76.68 , 76.72 , 76.77 , 76.81 , 76.86 , 76.90 , 76.95 , 76.99 , 77.04 , 77.08 , 77.13 , 77.17 , 77.22 , 77.26 , 77.31 , 77.35 , 77.40 , 77.44 , 77.49 , 77.53 , 77.58 , 77.62 , 77.67 , 77.71 , 77.76 , 77.80 , 77.85 , 77.89 , 77.94 , 78.04 , 78.08 , 78.12 , 78.17 , 78.21 , 78.25 , 78.29 , 78.34 , 78.38 , 78.42 , 78.47 , 78.51 , 78.55 , 78.60 , 78.64 , 78.68 , 78.72 , 78.77 , 78.81 , 78.85 , 78.89 , 78.94 , 78.98 , 79.02 , 79.07 , 79.11 , 79.15 , 79.19 , 79.24 , 79.28 , 79.32 , 79.37 , 79.41 , 79.45 , 79.50 , 79.54 , 79.58 , 79.62 , 79.67 , 79.71 , 79.75 , 79.79 , 79.89 , 79.93 , 79.97 , 80.01 , 80.05 , 80.10 , 80.14 , 80.18 , 80.22 , 80.26 , 80.30 , 80.34 , 80.38 , 80.42 , 80.46 , 80.50 , 80.55 , 80.59 , 80.63 , 80.67 , 80.71 , 80.75 , 80.79 , 80.83 , 80.87 , 80.91 , 80.95 , 81.00 , 81.04 , 81.08 , 81.12 , 81.16 , 81.20 , 81.24 , 81.28 , 81.32 , 81.36 , 81.40 , 81.44 , 81.49 , 81.53 , 81.57 , 81.61 , 81.65 , 81.69 , 81.73 , 81.77 , 81.81 , 81.85 , 81.89 , 81.94 , 81.98 , 82.02 , 82.06 , 82.10 , 82.14 , 82.18 , 82.22 , 82.26 , 82.30 , 82.35 , 82.39 , 82.43 , 82.47 , 82.51 , 82.55 , 82.59 , 82.63 , 82.67 , 82.71 , 82.75 , 82.80 , 82.84 , 82.88 , 82.92 , 82.96 , 83.00 , 83.04 , 83.08 , 83.12 , 83.16 , 83.20 , 83.24 , 83.29 , 83.33 , 83.37 , 83.41 , 83.45 , 83.44 , 83.48 , 83.52 , 83.57 , 83.61 , 83.65 , 83.70 , 83.74 , 83.78 , 83.82 , 83.87 , 83.91 , 83.95 , 84.00 , 84.04 , 84.08 , 84.12 , 84.17 , 84.21 , 84.25 , 84.30 , 84.34 , 84.38 , 84.42 , 84.47 , 84.51 , 84.55 , 84.60 , 84.64 , 84.68 , 84.72 , 84.77 , 84.81 , 84.85 , 84.90 , 84.94 , 84.98 , 85.02 , 85.07 , 85.11 , 85.15 , 85.20 , 85.24 , 85.28 , 85.32 , 85.37 , 85.41 , 85.45 , 85.49 , 85.54 , 85.58 , 85.62 , 85.67 , 85.71 , 85.75 , 85.80 , 85.84 , 85.88 , 85.92 , 85.97 , 86.01 , 86.05 , 86.09 , 86.14 , 86.18 , 86.22 , 86.27 , 86.31 , 86.35 , 86.39 , 86.44 , 86.48 , 86.52 , 86.57 , 86.61 , 86.65 , 86.70 , 86.74 , 86.78 , 86.82 , 86.87 , 86.91 , 86.95 , 86.99 , 87.06 , 87.11 , 87.15 , 87.19 , 87.23 , 87.27 , 87.32 , 87.36 , 87.40 , 87.44 , 87.48 , 87.53 , 87.57 , 87.61 , 87.65 , 87.69 , 87.73 , 87.78 , 87.82 , 87.86 , 87.90 , 87.94 , 87.99 , 88.03 , 88.07 , 88.11 , 88.15 , 88.20 , 88.24 , 88.28 , 88.32 , 88.36 , 88.40 , 88.45 , 88.49 , 88.53 , 88.57 , 88.61 , 88.66 , 88.70 , 88.74 , 88.78 , 88.82 , 88.86 , 88.91 , 88.95 , 88.99 , 89.03 , 89.07 , 89.12 , 89.16 , 89.20 , 89.24 , 89.28 , 89.33 , 89.37 , 89.41 , 89.45 , 89.49 , 89.53 , 89.58 , 89.62 , 89.66 , 89.70 , 89.74 , 89.79 , 89.83 , 89.87 , 89.91 , 89.95 , 90.00 , 90.04 , 90.08 , 90.12 , 90.16 , 90.20 , 90.25 , 90.29 , 90.33 , 90.37 , 90.41 , 90.46 , 90.50 , 90.54 , 90.58 , 90.62 , 90.66 , 90.71 , 90.75 , 90.79 , 90.83 , 90.87 , 90.92 , 90.96 , 91.00 , 91.04 , 91.08 , 91.13 , 91.17 , 91.21 , 91.25 , 91.29 , 91.33 , 91.38 , 91.42 , 91.46 , 91.50 , 91.54 , 91.59 , 91.63 , 91.67 , 91.71 , 91.75 , 91.80 , 91.84 , 91.88 , 91.92 , 91.96 , 92.00 , 92.05 , 92.09 , 92.13 , 92.17 , 92.21 , 92.26 , 92.30 , 92.34 , 92.38 , 92.42 , 92.46 , 92.51 , 92.55 , 92.59 , 92.63 , 92.67 , 92.72 , 92.76 , 92.80 , 92.84 , 92.88 , 92.93 , 92.97 , 93.01 , 93.05 , 93.09 , 93.13 , 93.18 , 93.22 , 93.26 , 93.30 , 93.34 , 93.39 , 93.43 , 93.47 , 93.51 , 93.55 , 93.60 , 93.64 , 93.68 , 93.72 , 93.76 , 93.80 , 93.85 , 93.89 , 93.93 , 93.97 , 94.01 , 94.06 , 94.10 , 94.14 , 94.18 , 94.22 , 94.26 , 94.31 , 94.35 , 94.39 , 94.43 , 94.47 , 94.52 , 94.56 , 94.60 , 94.64 , 94.68 , 94.73 , 94.77 , 94.81 , 94.85 , 94.89 , 94.93 , 94.98 , 95.02 , 95.06 , 95.10 , 95.14 , 95.19 , 95.23 , 95.27 , 95.31 , 95.35 , 95.39 , 95.44 , 95.48 , 95.52 , 95.56 , 95.60 , 95.65 , 95.69 , 95.73 , 95.77 , 95.81 , 95.86 , 95.90 , 95.94 , 95.98 , 96.02 , 96.06 , 96.11 , 96.15 , 96.19 , 96.23 , 96.27 , 96.32 , 96.36 , 96.40 , 96.44 , 96.48 , 96.53 , 96.57 , 96.61 , 96.65 , 96.69 , 96.73 , 96.78 , 96.82 , 96.86 , 96.90 , 96.94 , 96.99 , 97.03 , 97.07 , 97.11 , 97.15 , 97.20 , 97.24 , 97.28 , 97.32 , 97.36 , 97.40 , 97.45 , 97.49 , 97.53 , 97.57 , 97.61 , 97.66 , 97.70 , 97.74 , 97.78 , 97.82 , 97.89 , 97.93 , 97.97 , 98.01 , 98.05 , 98.10 , 98.14 , 98.18 , 98.22 , 98.26 , 98.30 , 98.34 , 98.38 , 98.42 , 98.46 , 98.50 , 98.55 , 98.59 , 98.63 , 98.67 , 98.71 , 98.75 , 98.79 , 98.83 , 98.87 , 98.91 , 98.95 , 99.00 , 99.04 , 99.08 , 99.12 , 99.16 , 99.20 , 99.24 , 99.28 , 99.32 , 99.36 , 99.40 , 99.45 , 99.49 , 99.53 , 99.57 , 99.61 , 99.65 , 99.71 , 99.75 , 99.80 , 99.84 , 99.88 , 99.92 , 99.96 , 99.99 , 100.03 , 100.07 , 100.12 , 100.16 , 100.20 , 100.24 , 100.28 , 100.31 , 100.35 , 100.39 , 100.43 , 100.48 , 100.52 , 100.56 , 100.60 , 100.63 , 100.67 , 100.71 , 100.75 , 100.80 , 100.84 , 100.88 , 100.92 , 100.96 , 100.99 , 101.03 , 101.07 , 101.12 , 101.16 , 101.20 , 101.24 , 101.28 , 101.31 , 101.35 , 101.39 , 101.43 , 101.48 , 101.41 , 101.45 , 101.50 , 101.54 , 101.59 , 101.63 , 101.67 , 101.72 , 101.76 , 101.80 , 101.85 , 101.89 , 101.94 , 101.98 , 102.02 , 102.07 , 102.11 , 102.16 , 102.20 , 102.24 , 102.29 , 102.33 , 102.38 , 102.42 , 102.46 , 102.51 , 102.55 , 102.60 , 102.64 , 102.68 , 102.73 , 102.77 , 102.81 , 102.86 , 102.90 , 102.95 , 102.99 , 103.03 , 103.08 , 103.12 , 103.17 , 103.26 , 103.31 , 103.35 , 103.39 , 103.43 , 103.47 , 103.52 , 103.56 , 103.60 , 103.64 , 103.68 , 103.73 , 103.77 , 103.81 , 103.85 , 103.89 , 103.93 , 103.98 , 104.02 , 104.06 , 104.10 , 104.14 , 104.19 , 104.23 , 104.27 , 104.31 , 104.35 , 104.39 , 104.44 , 104.48 , 104.52 , 104.56 , 104.60 , 104.65 , 104.69 , 104.73 , 104.77 , 104.81 , 104.86 , 104.90 , 104.94 , 104.98 , 105.02 , 105.12 , 105.16 , 105.20 , 105.24 , 105.28 , 105.32 , 105.36 , 105.39 , 105.43 , 105.48 , 105.52 , 105.56 , 105.60 , 105.64 , 105.68 , 105.71 , 105.75 , 105.80 , 105.84 , 105.88 , 105.92 , 105.96 , 106.00 , 106.03 , 106.07 , 106.12 , 106.16 , 106.20 , 106.24 , 106.28 , 106.32 , 106.36 , 106.39 , 106.43 , 106.48 , 106.52 , 106.56 , 106.60 , 106.64 , 106.68 , 106.71 , 106.75 , 106.80 , 106.84 , 106.88 , 106.89 , 106.93 , 106.97 , 107.01 , 107.05 , 107.10 , 107.14 , 107.18 , 107.22 , 107.26 , 107.30 , 107.34 , 107.38 , 107.42 , 107.46 , 107.50 , 107.55 , 107.59 , 107.63 , 107.67 , 107.71 , 107.75 , 107.79 , 107.83 , 107.87 , 107.91 , 107.95 , 108.00 , 108.04 , 108.08 , 108.12 , 108.16 , 108.20 , 108.24 , 108.28 , 108.32 , 108.36 , 108.40 , 108.45 , 108.49 , 108.53 , 108.57 , 108.61 , 108.65 , 108.66 , 108.71 , 108.75 , 108.79 , 108.83 , 108.87 , 108.92 , 108.96 , 109.00 , 109.04 , 109.08 , 109.13 , 109.17 , 109.21 , 109.25 , 109.29 , 109.33 , 109.38 , 109.42 , 109.46 , 109.50 , 109.54 , 109.59 , 109.63 , 109.67 , 109.71 , 109.75 , 109.80 , 109.84 , 109.88 , 109.92 , 109.96 , 110.00 , 110.05 , 110.09 , 110.13 , 110.17 , 110.21 , 110.26 , 110.30 , 110.34 , 110.38 , 110.42 , 110.44 , 110.48 , 110.52 , 110.57 , 110.61 , 110.65 , 110.70 , 110.74 , 110.78 , 110.82 , 110.87 , 110.91 , 110.95 , 111.00 , 111.04 , 111.08 , 111.12 , 111.17 , 111.21 , 111.25 , 111.30 , 111.34 , 111.38 , 111.42 , 111.47 , 111.51 , 111.55 , 111.60 , 111.64 , 111.68 , 111.72 , 111.77 , 111.81 , 111.85 , 111.90 , 111.94 , 111.98 , 112.02 , 112.07 , 112.11 , 112.15 , 112.20 , 112.31 , 112.35 , 112.39 , 112.43 , 112.48 , 112.52 , 112.56 , 112.59 , 112.63 , 112.67 , 112.71 , 112.75 , 112.80 , 112.84 , 112.88 , 112.91 , 112.95 , 112.99 , 113.03 , 113.07 , 113.12 , 113.16 , 113.20 , 113.23 , 113.27 , 113.31 , 113.35 , 113.39 , 113.43 , 113.48 , 113.52 , 113.56 , 113.59 , 113.63 , 113.67 , 113.71 , 113.75 , 113.80 , 113.84 , 113.88 , 113.91 , 113.95 , 113.99 , 114.03 , 114.07 , 114.12 , 114.16 , 114.20 , 114.24 , 114.28 , 114.32 , 114.36 , 114.39 , 114.43 , 114.48 , 114.52 , 114.56 , 114.60 , 114.64 , 114.68 , 114.71 , 114.75 , 114.80 , 114.84 , 114.88 , 114.92 , 114.96 , 115.00 , 115.03 , 115.07 , 115.12 , 115.16 , 115.20 , 115.24 , 115.28 , 115.32 , 115.36 , 115.39 , 115.43 , 115.48 , 115.52 , 115.56 , 115.60 , 115.64 , 115.68 , 115.71 , 115.75 , 115.80 ,
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

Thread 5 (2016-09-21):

Check magnetic field prior to calibration routine

SloMusti, 2016-09-21:
Prior to calibrating it would be good to implement a sanity check if magnetic field is sufficient and encoder generates valid results. Note the encoder may return magnetic field too high flag even if ti is too low.

jcchurch13, 2016-09-21:
Good thinking.  I'll add something to automatically check the encoder diagnostics when I get a chance.

SloMusti, 2016-09-27:
Based on #4 calibration routine should do a sanity check on the magnetic encoder values over one rotation, such that they change over the rotation for the full 16384 (2^14) range, else return a warning or error.

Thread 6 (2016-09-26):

Configuration defaults for different steppers/magnets

SloMusti, 2016-09-26:
Collect and document defaults for common configurations as a guide for assembling custom motor configurations.

I propose the following format or similar:
- motor type:
- magnet type:
- magnet to encoder distance
- PID values
- floatangle (not quite clear why/how different)
- any other variables possibly required

@jcchurch13 Can you please post your current working values for stepper motors and magnets you have.

minid33, 2016-10-29:
Additionally, I'd appreciate some help with steps/mm.

I have a smoothieboard, I was able to fix the stepper direction by reversing the pin in the config but when it comes to adjusting the steps/mm in the config it seems to make no difference, which leads me to believe this is a setting for the built in stepper drivers im bypassing.

I tried changing parameters.ccp dir to 0 and this did not reverse the direction of the stepper. The names of variables in this project could benefit from being a little more verbose.

How can I adjust the equivalent of steps/mm in this code? I was messing with spr in parameters.cpp and this seemingly had no effect.

jcchurch13, 2016-10-29:
I presume you have uncommented this line in the main loop to use the step/dir interface:
"r=0.1125*step_count" :
r is the control loop setpoint variable.  If you are in closed loop position mode, setting r = 45.3  will cause the Mechaduino to point to 45.3.
step_count is the running count of step commands received via the step/dir interface.  0.1125 is just the scale factor (0.1125 degrees per step)... this value happens to be 1.8/16, but you can change it to whatever you like.
-Joe

minid33, 2016-10-30:
That did the trick, thanks.

Closed 2017-01-05.

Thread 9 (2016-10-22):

Firmware Branches

Eriobis, 2016-10-22:
Hi,
Since the mechaduino have been released to public, it would be nice that your git tree contains the working firmware in the working branch, or maybe a tag with 0.1 written on it.
I had a hard time making it work ( i tried 3 steppers ) to make it work, until I used the developement branch.

jcchurch13, 2016-10-22:
Hi,
We have been keeping the "working" firmware in the multi-file branch which is set as the default.  The development branch is being used for development, so it is a little less stable.  If the multi-file branch is not working for you, let us know.
-Joe

Eriobis, 2016-10-23:
The motor was struggling and when I tried some commands everything disconnected. So I tried the developement branch.
Everything is smooth. Except 2 bugs, mayve I can open issues for that. Sometimes ( 1 on 3 ) times, the Y ( enable interrupt ) makes everything stop and the code just stop working.

Second, the "0" of the motor cannot be reached easily, it is oscilliating constantly even with a lower P or a less agressive Derivative.
I will let you know my developement as I make tests !

oddball1, 2016-10-29:
I dont understand how to download the Mechaduino 0.1 firmware to Arduino?. I purchased 3 of these stepper motors with the encoders and I'm stuck at this point, if i copy and paste the one file that says Mechaduino 0.1 and compile it, it says i'm missing the utils.h and errors out. Please any input would be appreciated as i am new to this.

minid33, 2016-10-29:
Try updating your version of the arduino ide @oddball1 I had an older version and it said I was missing stuff.

oddball1, 2016-10-29:
Thanks for the fast responce minid33, I am using the latest version 1.6.12, I think I'm not doing it correctly.
I can see the file, utils.h on the same page as the Mechaduino 0.1, but not sure if i'm supposed to include it some how. I have also tried anouther version of Arduino 1.6.10, it was the same result.

jcchurch13, 2016-10-29:
Hi oddball1,
Please download the entire repository from here (click "clone or download"):
[https://github.com/jcchurch13/Mechaduino-Firmware](url)

Then you will need to unzip the file and navigate to the Mechaduino_01 file.  Double clicking the Mechaduino_01 file should open all of the files in the Arduino IDE (There should be 11 tabs/files).

oddball1, 2016-10-31:
Thanks jcchurch13, thats exactly what I was doing wrong, I've never used this web page before so I had no idea how to down load this, Thanks again, very much appreciate your help.

oddball1, 2016-10-31:
Oh darn, spoke to soon, well not really, I don't get the same error ad can see all the tabs in Arduino,but now I get these errors, Arduino: 1.6.12 (Windows 10), Board: "Arduino/Genuino Zero (Programming Port)"

Sketch uses 98,608 bytes (37%) of program storage space. Maximum is 262,144 bytes.
Open On-Chip Debugger 0.9.0-gd4b7679 (2015-06-10-22:24)
Licensed under GNU GPL v2
For bug reports, read
	http://openocd.org/doc/doxygen/bugs.html
debug_level: 0
adapter speed: 500 kHz
adapter_nsrst_delay: 100
cortex_m reset_config sysresetreq
Error: unable to find CMSIS-DAP device
Error: No Valid JTAG Interface Configured.
Error: No Valid JTAG Interface Configured.

Invalid library found in C:\Users\Darrell\Documents\Arduino\libraries\Marlin-Marlin_v1: C:\Users\Darrell\Documents\Arduino\libraries\Marlin-Marlin_v1
Invalid library found in C:\Users\Darrell\Documents\Arduino\libraries\Marlin-Marlin_v1: C:\Users\Darrell\Documents\Arduino\libraries\Marlin-Marlin_v1

This report would have more information with
"Show verbose output during compilation"
option enabled in File -> Preferences.

bretskee, 2016-11-01:
Just quickly looked at you post and in board selection you should be using 'native USB port' instead of 'programming port'.

oddball1, 2016-11-03:
Thanks again for your help, just back to it tonight myself, so that did work, I was able to upload the firmware. I restarted my computer, checked the port it was in (com7) opened the serial on the called for baud rate and typed s and send, nothing, tried others like d and w, all nothing. I have a 5vdc power supply at 2amps, also measured voltage, should there be a power light on the board?
I was really hoping this would be a lot easier to do, I have this feeling I'm going to spend more time trying to get this up and running, I hope I'm wrong, when I saw the video on Kickstarter on how one stepper motor could control another one (like Simon says) this is why I backed the project, that's all I'm try to set up, I turn one stepper and the other follows exactly those steps. I am working on a product for patenting and could see your product being part of my product, in the thousands if not tens of thousands in the future, but really need to get this part up and running, any support you could offer would be greatly appreciated, thanks again for your time. Darrell Stein.

Sent from my iPhone

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

oddball1, 2016-11-06:
Does anyone have any sugestions on where i go form here? I can't seem to get these motors running, just paper weights at this time.

jcchurch13, 2016-11-06:
Hi oddball,

Can you give us any more information?  It sounds like you were able to successfully upload the firmware but you haven't been able to communicate over serial?  I'd try resetting/disconnecting and reconnecting the board a couple times.  You should be able to get a response from the board even without an external power supply.  You will need 8V to 25V on the screw terminals to provide power to the motor to get it to move though.  You only need to provide 5V to Vin if you are not using the USB.  (See the wiring diagrams here: http://tropical-labs.com/index.php/mechaduino)
The LED is not a power LED, you can program it to do whatever you like.
-Joe

oddball1, 2016-11-07:
Thanks jcchurch13 again, I'm just not sure what to do with these motors and boards, it just doesnt seem to be very easy to get them to work, I've had them for a bit now and can only get one step ahead every few days, I feel clearer instructions would certainly be helpful for those that are new to this type of system.
So now i have 12vdc to the board and the motor locks up now when its pluged into the usb port, but when i bring up the serial monitor and type "s" and enter, nothing happens, motor is still locked, i'm assuming i should have the mechaduino 01 program running in the arduino IDE. I have unpluged it several times, restarted the program and even tried all 3 motors and boards, and yes it seems that the firmware was successfully uploaded.

Electroradiography, 2016-11-07:
I have exactly the same issue with three motors. Is there a solution yet?

Bob

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

oddball1, 2016-11-08:
I guess not yet

jcchurch13, 2016-11-08:
Are you using the latest version of the "multi-file" branch?  Is it possible that "enableTCInterrupts()" is uncommented in the main file?  That's the only thing I can think of that might cause this behavior.  Sorry guys,  I haven't been able to replicate this issue, so I'm not really sure what else to suggest.

oddball1, 2016-11-08:
I hope so, it's the one you just sent me about a week ago.

Sent from my iPhone

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

Electroradiography, 2016-11-08:
Here are things I noticed when learning how to set up the Mechaduino:

It's not clear to me whether my boards have a bootloader. I ordered mine
from the Tropical
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
oddball1, 2016-11-08:
Thanks jcchurch13, could you please send the link!, when I go to the site I can't seem to find the download area, but when you sent the link last time it was clear where it was, thanks again.

Sent from my iPad

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

oddball1, 2016-11-08:
Thanks, I'll try to make some time tonight to try this. I will be looking for instructions on how to hook up two motors to control each other, like in your kickstarter video, when you turn one the other follows, just a heads up, thanks again, I know you have a lot on the go right now so I do appreciate this.

Sent from my iPad

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

Electroradiography, 2016-11-08:
That did it - Thanks Joe

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

oddball1, 2016-11-08:
me too, i was able to run the calibration, but unable to copy the 16 thousand plus numbers, i can get them highlighted as per the instructions, but right clicking on the mouse wont bring up the copy command and the short cut on the keyboard of Ctrl + C will not copy either?? any sugestions ?

oddball1, 2016-11-09:
ok, i guess ctrl c did copy it, and i got it into the parameters.cpp, ive calibrated all 3 motors now, woot woot.
Now my goal is to get one stepper to be able to control anouther stepper just like the video on Kickstarter, ideally i would like to control the movements of 6,8 or more stepper motors with one stepper as the master, so if the master was at say 18 degrees, the slaves would be the same. Any ideas on this anyone!

oddball1, 2016-11-12:
Now my goal is to get one stepper to be able to control anouther stepper just like the video on Kickstarter, ideally i would like to control the movements of 6,8 or more stepper motors with one stepper as the master, so if the master was at say 18 degrees, the slaves would be the same. Any ideas on this anyone!

jcchurch13, 2016-11-13:
Oddball1,
Please see the description in this video:  https://www.youtube.com/watch?v=rSugkwWcFOY
There are a number of ways that you can implement this.  The simplest way that I have found is to feed the current position of each motor into the other motor and use it as the setpoint of the position control loop.  You can use analog I/O pins to do this (but there are other ways too..I2C for example).  This set up will definitely involve some tuning/coding to get good performance.  Sorry, that's all the help I can offer at the moment.  I am very busy working on general firmware improvements.
Hope that helps,
Joe

oddball1, 2016-11-17:
Thanks, I really don't understand how to do this.

Electroradiography, 2016-11-17:
I need to use two 5v input signals to drive the motor. One signal will command clockwise motion for a few seconds then stop. The second signal will do the exact opposite. I can make the motor respond with the serial monitor but I'm not sure how to code my application. I'm afraid I will damage the Mechaduino code unless I know more about how it works. Is there a guide available to help me?

jcchurch13, 2016-11-18:
We're working on putting together some more documentation.  Please stay tuned!
-Joe

oddball1, 2016-11-19:
That would be nice, then I could use them,  hopefully you will include how to have one drive another like in your video, I egearly await .

oddball1, 2017-04-24:
Any documintations yet on hooking up two motors like in the video I saw when I backed this project on kick starters?? You show one motor controlling another one, back in January you mentioned you would be putting something together

jcchurch13, 2017-04-28:
To accomplish the electronic gearing shown in the video, you can have the position loop setpoint controlled by an analog input on both motors, and set an analog output pin proportional to the encoder reading on each motor.  Then just feed the analog position output from each motor into the setpoint input of the other.  Please see the Mechaduino Manual that we added to in the repo for examples of how to configure inputs/outputs/control loop setpoints.  This configuration will definitely require some tuning/filtering depending on how you want it to behave.  I haven't published a detailed description of how to do this yet because though conceptually simple, it takes a certain amount of experimentation depending on exactly how you want it to behave.  Also, I think there may be better, more sophisticated ways to set this up (using, say I2C instead of analog setpoints), but I haven't had time to develop this.  We've been focusing on trying to keep the hardware available and make general improvements to the firmware.  I encourage you to experiment with the set up I described above.  It's not that hard to get it up and running, but its not as simple as just running a certain piece of code.

Closed 2017-01-05.

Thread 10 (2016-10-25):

USB serial communications lock up

rreilink, 2016-10-25:
I just received my Kickstarter Mechaduinos. I have flashed the Mechaduino_01 firmware. Using the serial monitor, I can give a few commands to make it move (I did perform the calibration first). However, after a few commands the communication locks up. Actually, it causes even the Arduino PC application to hang. The only thing to make it work again is unplug/replug the USB connector.

The issue occurs both in Mac OS X and in Windows 7. On Mac OS X I have used both the Arduino PC application and Minicom as serial terminal applications. In all cases I get the same result. Is this a known firmware issue?

ericmoderbacher, 2016-10-27:
BUMP.  I experienced the same issue on Mac OS X.  Have not tried windows.

Eriobis, 2016-10-29:
Same issue here, I've found that if I enable the interrupt before choosing the mode, everything stalls ( the communication )

ericmoderbacher, 2016-11-08:
is this fixed by the "SerialCheck must be uncommented in loop" check in?[https://github.com/jcchurch13/Mechaduino-Firmware/commit/59ae0f516e6fb6f75cfc882bbd4a4016c0681eee](url)

jcchurch13, 2016-11-09:
I'm not sure.  It sounds like you are able to get the Serial monitor to work up to a certain point.  (That fix was for a completely unresponsive serial monitor.)  Can you provide some more details about when it stalls?  The commands 's' and 'd' will not work properly if you are in closed loop mode (interrupt enabled).

ericmoderbacher, 2016-11-12:
I had some time to try out the mechadinos again.  I'm not experiencing the communications issue anymore.  Thanks!

Closed 2017-01-05.

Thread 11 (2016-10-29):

On board installed resistor

Eriobis, 2016-10-29:
In the code you have :
const float rSense = 0.150;

In one schematic you wrote 0.250.
Can you confirm that it's .150 that are installed on mechaduino 0.1 ??

Thanks

jcchurch13, 2016-10-29:
That's correct, it should be 0.15 on the Mechaduino 0.1.

Closed 2016-11-30.

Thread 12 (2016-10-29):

Question about magic values

Eriobis, 2016-10-29:
In the Interrupt routine, I would like to know the number 150 ( in mode x ) and number 200 ( in mode v )
What do they represent ??? ( Ill do a define for those numbers )

```
switch (mode) {
  case 'x':
    e = (r - yw);
    SerialUSB.print(y);
    SerialUSB.print(";");
    SerialUSB.print(e);
    SerialUSB.println(";");
    ITerm += (pKi * e);
    if (ITerm > 150) ITerm = 150;
    else if (ITerm < -150) ITerm = -150;
    u = ((pKp * e) + ITerm - (pKd * (yw - yw_1))); //ARDUINO library style
    //u = u+lookup_force(a)-20;
    //   u = u_1 + cA*e + cB*e_1 + cC*e_2;     //ppt linked in octave script
    //  u = 20*e;//
    break;

  case 'v':
    e = (r - ((yw - yw_1) * Fs*0.16666667));//error in degrees per rpm (sample frequency in Hz * (60 seconds/min) / (360 degrees/rev) )
    ITerm += (vKi * e);
    if (ITerm > 200) ITerm = 200;
    else if (ITerm < -200) ITerm = -200;
    u = ((vKp * e) + ITerm - (vKd * (yw - yw_1)));//+ lookup_force(a)-20; //ARDUINO library style
    break;
```

jcchurch13, 2016-10-29:
Those are integral windup limits:
https://en.wikipedia.org/wiki/Integral_windup

Closed 2017-01-05.

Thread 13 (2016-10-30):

Feature request: PID Autotuning

minid33, 2016-10-30:
I'm just about to kick off a print for the first time and I can't help but feel like my PIDs are going to be innacurate, maybe even hugely inacurate.

PID autotuning is an obvious answer to this problem to get into the ballpark of a good tune. I'd love this to be implemented in future releases.

minid33, 2016-11-26:
Discussed further here, https://groups.google.com/forum/#!topic/mechaduino/29lYo7xKL8Q
Has been implemented in a fork

Kaiwol1990, 2017-01-10:
Hi minid33,

it's not a real fork anymore. I've changed quiet a bit in my firmware version, maybe give it a try and send me some feedback.
You can also use the PID setting you get with my firmware but have to recalculate them for this firmwareversion. To do that you have to considere the different frequencys. Here's how you can calculate them from my firmware to the this one.

Kp = Kp_my_version
Ki = Ki_my_version * (FPID / FPID_my_version)
Kd = Kd_my_version* (FPID_my_version / FPID)

if you take a look at my firmware you can also use the dev branch. I've implemented filtering, feedforward, friction compensation and inertia copensation. But there's no autotune for those variables.
If your familiar with such things give it a try.

- Kai

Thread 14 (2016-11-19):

Configuration to work with 0.9 degree steppers.

OKRobotics, 2016-11-19:
I have been reading through all the other posts, and it looks like these boards should be able to drive 0.9 degree steppers. The only information that I have found about it is that spr needs to be set to 400 instead of 200 in the Parameters.cpp file. I have done that, and the motor now runs through all 400 steps during calibration, and will move fine in open loop mode, but when put into closed loop mode, it fails. The same board and magnet works fine on a 1.8 degree stepper with spr set to 200. Any ideas?

Apehand, 2016-11-22:
Hey there.
I'm running in the same problem. Do you have any solutions jet? Greetings.

jcchurch13, 2016-11-22:
Hi,
There are a couple of numbers that will need to be changed in the output() function in the utils.cpp file.  I'm working on an updated version of the firmware that should fix this issue.
-Joe

Apehand, 2016-11-23:
Hey Joe, do you have any values for testing? It is a quite annoying problem.

jcchurch13, 2016-11-23:
I've updated the firmware and confirmed that it works on a 0.9 degree stepper.  All you need to do is set spr = 400 in parameters.cpp, and set PA = 0.9 in State.cpp.

-Joe

Apehand, 2016-11-25:
I tested it today and I think it is now working properly. Thank you a lot. It is a amazing work!

Closed 2016-11-30.

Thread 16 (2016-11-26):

Odd conditional check in output() function

mikeanton, 2016-11-26:
In the output() function, there is this piece of code:
```
  if (sin_coil_A > 1024) {
    sin_coil_A = sin_coil_A - 65536;
  }
```
The variable sin_coil_A is declared as an int.  On an ARM processor, this is 4 bytes, or the equivalent of a long on smaller Arduinos.  So, if the value is larger than 1024, say 1025 as an example, you would end up with a result of -64511.  I'm not sure what this is supposed to accomplish, or why you would even need to do it.  Since this value is directly looked up from the sin table, and you have control over the magnitude of the table, why do you need to attempt some sort of saturation?  Even if the variable was only two bytes, it would give a result that was unchanged from what you started with, i.e. if sin_coil_A = 1025, the result of 1025 - 65536 = 1025.

Note that since an int on this architecture is 4 bytes, that your sin table takes up 14400 bytes of RAM (almost half).  You could declare it as 'short int' instead, which would give you two byte ints.  There is sometimes a speed penalty when accessing these however, as ARMs prefer to work in their word size.  Or, you could store your sin table with much higher resolution than you currently are, though there might not be much point if the DAC resolution is limited.

At any rate, I don't think this does what you intended it to do.

jcchurch13, 2016-11-26:
Thanks Mike,  this code is no longer necessary and should have been removed!  I will upload an updated version of the code shortly.

Closed 2016-11-26.

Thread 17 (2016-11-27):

Missing file include and invalid type.

Razaekel, 2016-11-27:
Controller.cpp has a '#include <SPI.h>' but that include is not included in Mechaduino_01.ino, which gives an error on compiling.

After adding '#include "SPI.h"' to the .ino, it gives a ''PROGMEM' does not name a type' error in Parameters.h. Additionally, from what I can find out about PROGMEM in the Arduino, it's only supported in the AVR architecture.

Razaekel, 2016-11-27:
After removing the references to PROGMEM, it  gave another error about a missing "Wire.h". After adding this include to the .ino, it compiled fine.

mikeanton, 2016-11-27:
I'm pretty sure I had to upgrade to the most recent Arduino IDE (1.6.12), and then it compiled fine.  I had problems like this as well using a slightly older version (1.6.5).

Razaekel, 2016-11-27:
@mikeanton You are correct, updating to the latest Arduino IDE (1.6.13) allows it to compile.

This IDE version requirement should be mentioned in the README.

Closing this issue, as it's no longer valid.

Closed 2016-11-27.

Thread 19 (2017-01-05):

Reorganize as an Arduino library

lukecyca, 2017-01-05:
The Mechaduino firmware should be organized as a library with example sketches, rather than a single monolithic firmware sketch. This would allow Mechaduino to be used as a platform that can adapt to various use-cases.

It is great that the current firmware keeps `setup()` and `loop()` so minimal, and does most of the work elsewhere. This makes it easy to add higher-level application-specific code. However it currently requires modifying `Mechaduino_01.ino`, and so it lacks separation and makes it more difficult to maintain multiple application-specific sketches, or to pull changes when the firmware is improved.

It would be better if the Mechaduino was an Arduino library, allowing it to be included in other sketches. Arduino libraries have an `examples` folder which would include the current `Mechaduino_01.ino` as a basic example. Other example sketches could be used for things like auto-tuning, so that the core library wouldn't need to become monolithic.

ryanaltair, 2017-01-16:
this is really a good idea and I am trying.

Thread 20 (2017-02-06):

invalid type argument of '->' (have 'uint16_t')

pearl-qeautomation, 2017-02-06:
Just cloned the latest version and trying to upload to my Mechaduino and getting an `invalid type argument of '->' (have 'uint16_t')` error.

```
Arduino: 1.8.1 (Mac OS X), Board: "Arduino/Genuino Uno"

/Applications/Arduino.app/Contents/Java/arduino-builder -dump-prefs -logger=machine -hardware /Applications/Arduino.app/Contents/Java/hardware -hardware /Users/allen/Library/Arduino15/packages -hardware /Users/allen/Documents/Arduino/hardware -tools /Applications/Arduino.app/Contents/Java/tools-builder -tools /Applications/Arduino.app/Contents/Java/hardware/tools/avr -tools /Users/allen/Library/Arduino15/packages -built-in-libraries /Applications/Arduino.app/Contents/Java/libraries -libraries /Users/allen/Documents/Arduino/libraries -fqbn=arduino:avr:uno -ide-version=10801 -build-path /var/folders/_y/wxctgwss5zv1fq27s5hw50zr0000gn/T/arduino_build_11632 -warnings=all -prefs=build.warn_data_percentage=75 -prefs=runtime.tools.avrdude.path=/Users/allen/Library/Arduino15/packages/arduino/tools/avrdude/6.0.1-arduino5 -prefs=runtime.tools.avr-gcc.path=/Applications/Arduino.app/Contents/Java/hardware/tools/avr -verbose /Users/allen/code/Mechaduino-Firmware/Mechaduino_01/Mechaduino_01/Mechaduino_01.ino
/Applications/Arduino.app/Contents/Java/arduino-builder -compile -logger=machine -hardware /Applications/Arduino.app/Contents/Java/hardware -hardware /Users/allen/Library/Arduino15/packages -hardware /Users/allen/Documents/Arduino/hardware -tools /Applications/Arduino.app/Contents/Java/tools-builder -tools /Applications/Arduino.app/Contents/Java/hardware/tools/avr -tools /Users/allen/Library/Arduino15/packages -built-in-libraries /Applications/Arduino.app/Contents/Java/libraries -libraries /Users/allen/Documents/Arduino/libraries -fqbn=arduino:avr:uno -ide-version=10801 -build-path /var/folders/_y/wxctgwss5zv1fq27s5hw50zr0000gn/T/arduino_build_11632 -warnings=all -prefs=build.warn_data_percentage=75 -prefs=runtime.tools.avrdude.path=/Users/allen/Library/Arduino15/packages/arduino/tools/avrdude/6.0.1-arduino5 -prefs=runtime.tools.avr-gcc.path=/Applications/Arduino.app/Contents/Java/hardware/tools/avr -verbose /Users/allen/code/Mechaduino-Firmware/Mechaduino_01/Mechaduino_01/Mechaduino_01.ino
Using board 'uno' from platform in folder: /Users/allen/Library/Arduino15/packages/arduino/hardware/avr/1.6.13
Using core 'arduino' from platform in folder: /Users/allen/Library/Arduino15/packages/arduino/hardware/avr/1.6.13
Build options changed, rebuilding all
Detecting libraries used...
"/Applications/Arduino.app/Contents/Java/hardware/tools/avr/bin/avr-g++" -c -g -Os -w -std=gnu++11 -fpermissive -fno-exceptions -ffunction-sections -fdata-sections -fno-threadsafe-statics  -flto -w -x c++ -E -CC -mmcu=atmega328p -DF_CPU=16000000L -DARDUINO=10801 -DARDUINO_AVR_UNO -DARDUINO_ARCH_AVR   "-I/Users/allen/Library/Arduino15/packages/arduino/hardware/avr/1.6.13/cores/arduino" "-I/Users/allen/Library/Arduino15/packages/arduino/hardware/avr/1.6.13/variants/standard" "/var/folders/_y/wxctgwss5zv1fq27s5hw50zr0000gn/T/arduino_build_11632/sketch/Mechaduino_01.ino.cpp" -o "/dev/null"
"/Applications/Arduino.app/Contents/Java/hardware/tools/avr/bin/avr-g++" -c -g -Os -w -std=gnu++11 -fpermissive -fno-exceptions -ffunction-sections -fdata-sections -fno-threadsafe-statics  -flto -w -x c++ -E -CC -mmcu=atmega328p -DF_CPU=16000000L -DARDUINO=10801 -DARDUINO_AVR_UNO -DARDUINO_ARCH_AVR   "-I/Users/allen/Library/Arduino15/packages/arduino/hardware/avr/1.6.13/cores/arduino" "-I/Users/allen/Library/Arduino15/packages/arduino/hardware/avr/1.6.13/variants/standard" "/var/folders/_y/wxctgwss5zv1fq27s5hw50zr0000gn/T/arduino_build_11632/sketch/Controller.cpp" -o "/dev/null"
"/Applications/Arduino.app/Contents/Java/hardware/tools/avr/bin/avr-g++" -c -g -Os -w -std=gnu++11 -fpermissive -fno-exceptions -ffunction-sections -fdata-sections -fno-threadsafe-statics  -flto -w -x c++ -E -CC -mmcu=atmega328p -DF_CPU=16000000L -DARDUINO=10801 -DARDUINO_AVR_UNO -DARDUINO_ARCH_AVR   "-I/Users/allen/Library/Arduino15/packages/arduino/hardware/avr/1.6.13/cores/arduino" "-I/Users/allen/Library/Arduino15/packages/arduino/hardware/avr/1.6.13/variants/standard" "-I/Users/allen/Library/Arduino15/packages/arduino/hardware/avr/1.6.13/libraries/SPI/src" "/var/folders/_y/wxctgwss5zv1fq27s5hw50zr0000gn/T/arduino_build_11632/sketch/Controller.cpp" -o "/dev/null"
"/Applications/Arduino.app/Contents/Java/hardware/tools/avr/bin/avr-g++" -c -g -Os -w -std=gnu++11 -fpermissive -fno-exceptions -ffunction-sections -fdata-sections -fno-threadsafe-statics  -flto -w -x c++ -E -CC -mmcu=atmega328p -DF_CPU=16000000L -DARDUINO=10801 -DARDUINO_AVR_UNO -DARDUINO_ARCH_AVR   "-I/Users/allen/Library/Arduino15/packages/arduino/hardware/avr/1.6.13/cores/arduino" "-I/Users/allen/Library/Arduino15/packages/arduino/hardware/avr/1.6.13/variants/standard" "-I/Users/allen/Library/Arduino15/packages/arduino/hardware/avr/1.6.13/libraries/SPI/src" "/var/folders/_y/wxctgwss5zv1fq27s5hw50zr0000gn/T/arduino_build_11632/sketch/Parameters.cpp" -o "/dev/null"
"/Applications/Arduino.app/Contents/Java/hardware/tools/avr/bin/avr-g++" -c -g -Os -w -std=gnu++11 -fpermissive -fno-exceptions -ffunction-sections -fdata-sections -fno-threadsafe-statics  -flto -w -x c++ -E -CC -mmcu=atmega328p -DF_CPU=16000000L -DARDUINO=10801 -DARDUINO_AVR_UNO -DARDUINO_ARCH_AVR   "-I/Users/allen/Library/Arduino15/packages/arduino/hardware/avr/1.6.13/cores/arduino" "-I/Users/allen/Library/Arduino15/packages/arduino/hardware/avr/1.6.13/variants/standard" "-I/Users/allen/Library/Arduino15/packages/arduino/hardware/avr/1.6.13/libraries/SPI/src" "-I/Users/allen/Library/Arduino15/packages/arduino/hardware/avr/1.6.13/libraries/Wire/src" "/var/folders/_y/wxctgwss5zv1fq27s5hw50zr0000gn/T/arduino_build_11632/sketch/Parameters.cpp" -o "/dev/null"
"/Applications/Arduino.app/Contents/Java/hardware/tools/avr/bin/avr-g++" -c -g -Os -w -std=gnu++11 -fpermissive -fno-exceptions -ffunction-sections -fdata-sections -fno-threadsafe-statics  -flto -w -x c++ -E -CC -mmcu=atmega328p -DF_CPU=16000000L -DARDUINO=10801 -DARDUINO_AVR_UNO -DARDUINO_ARCH_AVR   "-I/Users/allen/Library/Arduino15/packages/arduino/hardware/avr/1.6.13/cores/arduino" "-I/Users/allen/Library/Arduino15/packages/arduino/hardware/avr/1.6.13/variants/standard" "-I/Users/allen/Library/Arduino15/packages/arduino/hardware/avr/1.6.13/libraries/SPI/src" "-I/Users/allen/Library/Arduino15/packages/arduino/hardware/avr/1.6.13/libraries/Wire/src" "/var/folders/_y/wxctgwss5zv1fq27s5hw50zr0000gn/T/arduino_build_11632/sketch/State.cpp" -o "/dev/null"
"/Applications/Arduino.app/Contents/Java/hardware/tools/avr/bin/avr-g++" -c -g -Os -w -std=gnu++11 -fpermissive -fno-exceptions -ffunction-sections -fdata-sections -fno-threadsafe-statics  -flto -w -x c++ -E -CC -mmcu=atmega328p -DF_CPU=16000000L -DARDUINO=10801 -DARDUINO_AVR_UNO -DARDUINO_ARCH_AVR   "-I/Users/allen/Library/Arduino15/packages/arduino/hardware/avr/1.6.13/cores/arduino" "-I/Users/allen/Library/Arduino15/packages/arduino/hardware/avr/1.6.13/variants/standard" "-I/Users/allen/Library/Arduino15/packages/arduino/hardware/avr/1.6.13/libraries/SPI/src" "-I/Users/allen/Library/Arduino15/packages/arduino/hardware/avr/1.6.13/libraries/Wire/src" "/var/folders/_y/wxctgwss5zv1fq27s5hw50zr0000gn/T/arduino_build_11632/sketch/Utils.cpp" -o "/dev/null"
"/Applications/Arduino.app/Contents/Java/hardware/tools/avr/bin/avr-g++" -c -g -Os -w -std=gnu++11 -fpermissive -fno-exceptions -ffunction-sections -fdata-sections -fno-threadsafe-statics  -flto -w -x c++ -E -CC -mmcu=atmega328p -DF_CPU=16000000L -DARDUINO=10801 -DARDUINO_AVR_UNO -DARDUINO_ARCH_AVR   "-I/Users/allen/Library/Arduino15/packages/arduino/hardware/avr/1.6.13/cores/arduino" "-I/Users/allen/Library/Arduino15/packages/arduino/hardware/avr/1.6.13/variants/standard" "-I/Users/allen/Library/Arduino15/packages/arduino/hardware/avr/1.6.13/libraries/SPI/src" "-I/Users/allen/Library/Arduino15/packages/arduino/hardware/avr/1.6.13/libraries/Wire/src" "/var/folders/_y/wxctgwss5zv1fq27s5hw50zr0000gn/T/arduino_build_11632/sketch/analogFastWrite.c" -o "/dev/null"
"/Applications/Arduino.app/Contents/Java/hardware/tools/avr/bin/avr-g++" -c -g -Os -w -std=gnu++11 -fpermissive -fno-exceptions -ffunction-sections -fdata-sections -fno-threadsafe-statics  -flto -w -x c++ -E -CC -mmcu=atmega328p -DF_CPU=16000000L -DARDUINO=10801 -DARDUINO_AVR_UNO -DARDUINO_ARCH_AVR   "-I/Users/allen/Library/Arduino15/packages/arduino/hardware/avr/1.6.13/cores/arduino" "-I/Users/allen/Library/Arduino15/packages/arduino/hardware/avr/1.6.13/variants/standard" "-I/Users/allen/Library/Arduino15/packages/arduino/hardware/avr/1.6.13/libraries/SPI/src" "-I/Users/allen/Library/Arduino15/packages/arduino/hardware/avr/1.6.13/libraries/Wire/src" "/Users/allen/Library/Arduino15/packages/arduino/hardware/avr/1.6.13/libraries/SPI/src/SPI.cpp" -o "/dev/null"
"/Applications/Arduino.app/Contents/Java/hardware/tools/avr/bin/avr-g++" -c -g -Os -w -std=gnu++11 -fpermissive -fno-exceptions -ffunction-sections -fdata-sections -fno-threadsafe-statics  -flto -w -x c++ -E -CC -mmcu=atmega328p -DF_CPU=16000000L -DARDUINO=10801 -DARDUINO_AVR_UNO -DARDUINO_ARCH_AVR   "-I/Users/allen/Library/Arduino15/packages/arduino/hardware/avr/1.6.13/cores/arduino" "-I/Users/allen/Library/Arduino15/packages/arduino/hardware/avr/1.6.13/variants/standard" "-I/Users/allen/Library/Arduino15/packages/arduino/hardware/avr/1.6.13/libraries/SPI/src" "-I/Users/allen/Library/Arduino15/packages/arduino/hardware/avr/1.6.13/libraries/Wire/src" "/Users/allen/Library/Arduino15/packages/arduino/hardware/avr/1.6.13/libraries/Wire/src/Wire.cpp" -o "/dev/null"
"/Applications/Arduino.app/Contents/Java/hardware/tools/avr/bin/avr-g++" -c -g -Os -w -std=gnu++11 -fpermissive -fno-exceptions -ffunction-sections -fdata-sections -fno-threadsafe-statics  -flto -w -x c++ -E -CC -mmcu=atmega328p -DF_CPU=16000000L -DARDUINO=10801 -DARDUINO_AVR_UNO -DARDUINO_ARCH_AVR   "-I/Users/allen/Library/Arduino15/packages/arduino/hardware/avr/1.6.13/cores/arduino" "-I/Users/allen/Library/Arduino15/packages/arduino/hardware/avr/1.6.13/variants/standard" "-I/Users/allen/Library/Arduino15/packages/arduino/hardware/avr/1.6.13/libraries/SPI/src" "-I/Users/allen/Library/Arduino15/packages/arduino/hardware/avr/1.6.13/libraries/Wire/src" "/Users/allen/Library/Arduino15/packages/arduino/hardware/avr/1.6.13/libraries/Wire/src/utility/twi.c" -o "/dev/null"
Generating function prototypes...
"/Applications/Arduino.app/Contents/Java/hardware/tools/avr/bin/avr-g++" -c -g -Os -w -std=gnu++11 -fpermissive -fno-exceptions -ffunction-sections -fdata-sections -fno-threadsafe-statics  -flto -w -x c++ -E -CC -mmcu=atmega328p -DF_CPU=16000000L -DARDUINO=10801 -DARDUINO_AVR_UNO -DARDUINO_ARCH_AVR   "-I/Users/allen/Library/Arduino15/packages/arduino/hardware/avr/1.6.13/cores/arduino" "-I/Users/allen/Library/Arduino15/packages/arduino/hardware/avr/1.6.13/variants/standard" "-I/Users/allen/Library/Arduino15/packages/arduino/hardware/avr/1.6.13/libraries/SPI/src" "-I/Users/allen/Library/Arduino15/packages/arduino/hardware/avr/1.6.13/libraries/Wire/src" "/var/folders/_y/wxctgwss5zv1fq27s5hw50zr0000gn/T/arduino_build_11632/sketch/Mechaduino_01.ino.cpp" -o "/var/folders/_y/wxctgwss5zv1fq27s5hw50zr0000gn/T/arduino_build_11632/preproc/ctags_target_for_gcc_minus_e.cpp"
"/Applications/Arduino.app/Contents/Java/tools-builder/ctags/5.8-arduino11/ctags" -u --language-force=c++ -f - --c++-kinds=svpf --fields=KSTtzns --line-directives "/var/folders/_y/wxctgwss5zv1fq27s5hw50zr0000gn/T/arduino_build_11632/preproc/ctags_target_for_gcc_minus_e.cpp"
Compiling sketch...
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

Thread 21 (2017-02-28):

Weird issue with driver heating up and onboard led turning off.

RobWks, 2017-02-28:
Hey everyone,

So, finally got around to setting up two mechaduino's and I've run into the same issue with both. I can run the calibration for the mechaduino fine and paste the lookup values to Parameters.cpp -> const float lookup[] ={}. For testing I commented out `digitalWrite(ledPin,LOW);         // turn LED off ` so that the LED would remain on. I can move the stepper around with single steps using 's', but when I go to closed loop position mode by sending 'x' then 'y' over the serial monitor, the led turns off when I send 'y' and the motor driver gets too hot to touch for longer than a couple seconds. When I try to send 'r' to enter a new step point, it asks me to "Enter setpoint:", which I can do and it prints the value entered back at me, but the stepper doesn't move for any input. Is the LED going out an indication of some sort of issue? Is something shorting?  Any help is appreciated!

jcchurch13, 2017-02-28:
This sounds like an issue with the cal tables.  Can you double check that your cal tables consist of steadily increasing values.  Each entry should increase by roughly 0.02, and the table will wrap around to zero once it reaches 360.   If yours does not do this, try re-calibrating.  If the problem persists let me know.

RobWks, 2017-02-28:
Hey Joe, yes looks like that was the issue. Looking through the cal table I noticed that each entry was increasing by roughly 0.04. Made me realize that the random stepper I grabbed was actually 400 steps/rev instead of 200 steps/rev. Fixed the spr variable to be 400 and that fixed it. Thanks a lot!

Closed 2017-02-28.

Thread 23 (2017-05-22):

Unusable lookup table

haley0918, 2017-05-22:
I'm opening an issue here as I had no reply for my post at Google Groups.

 I have v0.1 hardware using the latest firmware from master branch.

Most of the time when I do calibration, the generated lookup table is unusable with the angle not changing at the beginning and end of the table. The angle only increase by 0.01 degree around middle of the table.

Occasionally I do get correct lookup table with about 0.02 degree increments.

I had checked through the encoder readouts and there are no problem.

[bad lookup table.txt](https://github.com/jcchurch13/Mechaduino-Firmware/files/1018754/bad.lookup.table.txt)

[good lookup table.txt](https://github.com/jcchurch13/Mechaduino-Firmware/files/1018750/good.lookup.table.txt)

What could be causing my Mechaduino to get bad lookup table almost all of the time?

jcchurch13, 2017-05-23:
That's strange.  Can you try uncommenting line 193 in utils.cpp and commenting lines 194 & 195 to help debug this issue?
```
   193    // SerialUSB.println(fullStepReadings[x], DEC);      //print readings as a sanity check
   194    SerialUSB.print(100.0*x/spr,1);
   195    SerialUSB.println("%");
```

haley0918, 2017-05-24:
Here's the debug log of the full step readings. On closer inspection, the count sequence below doesn't look right to me.

`16131
16218
16305
14743
79
166
253
329
`

Could this be the cause? If so, what is causing this?

[debug_log_0.txt](https://github.com/jcchurch13/Mechaduino-Firmware/files/1024535/debug_log_0.txt)

jcchurch13, 2017-05-24:
Ok,  I think I see what's happening.  The calibration routine averages 10 readings at each full step location, and it looks like your setup has a full step right near the encoder's 16383/0 transition.  For that one full step,  the code averages values on either side of that transition, leading to the false intermediate value of 14743 (which throws off the whole cal routine).  This is definitely a bug, and I'll try to patch this in the next day or so.   In the mean time, you can try rotating your board a tiny bit, or removing the averaging by setting avg = 1 in the calibration routine in Utils.cpp.

Thanks for reporting this issue!

haley0918, 2017-05-25:
Thanks for looking into this.

Would it be better to add a delay for each full step before taking readings? I'm thinking possibly either the shaft was oscillating or the encoder haven't caught up to a particular full step.  So maybe a delay to let the shaft settle at new step and let the encoder catch up?

Will look forward to your patch.

jcchurch13, 2017-05-31:
Ok, this issue should be fixed now!

Closed 2017-05-31.

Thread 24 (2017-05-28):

more sophisticated serial control

davidelang, 2017-05-28:
I've been working with a couple of other advanced motor control projects (maslowcnc which uses brushed DC motors and encoders, odrive which uses high power brushless DC motors and encoders, pthat which can do very high speed stepper motor driving) that all need something more than the traditional step/direction interface. To be clear, I am not a part of the development team of any of these, just a user/community participant.

As I'm seeing multiple projects with similar needs, I'm trying to see if it's possible to create a standard so that getting the smarter protocol implemented in managing software (Initially I'm aiming at linuxCNC adn grbl) easier, on the basis that implementing one protocol will support multiple hardware offering.

PTHat has a well defined serial API at http://pthat.com/index.php/command-set/. I'm suggesting to different projects that if that they can implement something compatible, it would be easier to get good support from CNC software.

One addition to the pthat command that would be needed is a way to synchronize the execution of commands across multiple controllers. To do this, I am suggesting that one GPIO pin be connected to a common bus (with a pull-up resistor), under normal conditions, each controller would pull the pin low. When they are issued a 'delayed start' command, they would switch the pin to an input pin and wait for it to go high. Once every controller on the bus does this, the pin will go high and they all start executing simultaniously (and a short time later, pull the pin low again as they start moving). This can both serve as the initial synchronized start, and be scattered in every so often to make sure that the clocks of different boards haven't drifted.

This will allow coordinated moves to happen across motors managed by different controllers, be they several mechaduino board, or some managed by one type of board and others managed by other types of boards.

Is this something that you would be interested in participating in by implementing a subset of the pthat commands? (one axis, without the aux/adc commands)

osresearch, 2018-06-18:
I'm working on a simplistic gcode interpreter for the MechaDuino: https://github.com/jcchurch13/Mechaduino-Firmware/compare/master...osresearch:master

As of now it supports a few common commands: https://github.com/osresearch/Mechaduino-Firmware/issues/1

Synchronizing multiple motors is something that we'll need. My thought was to use a multi-drop serial protocol instead and have the controller be able to send a "`G1 Xxxx Yyyy Zzzz F`" command so that it would reach all of them simultaneously and the commands like `M114` would be repeated for each axis to tell the device that it could transmit on the bus.

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

For my current whiteboard plotter I'm using separate USB ports for each motor and having the external controller dole out the points one a time to ensure that they remain synchronized.  It does not require microsecond level precision, so the USB latencies are fine.

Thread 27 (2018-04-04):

Licensing Questions

jceipek, 2018-04-04:
I'm evaluating the Mechaduino for use in a client project, and it's very promising so far. However, I'm a bit confused by how the licensing is intended to work as it relates to commercial projects.

I'm a huge fan of the open source community, and I try to release my own software projects under the MIT license where possible, particularly in situations where my code can easily be adapted for use by others.

Crerative Commons recommends against using CC licenses for software, see https://creativecommons.org/faq/#can-i-apply-a-creative-commons-license-to-software, and as such, I have some questions related to using a Mechaduino in a bespoke client project where I have to assign copyright to the client:

1. The Share Alike provision implies that all modifications must be released under the same license. What is your intent here? Because of how the Mechaduino code is structured, basically every project that uses it needs custom modifications to the parameters and to the Mechaduino.ino file which are essentially useless to everyone else. Do you want everyone to share these types of changes?

2. The Mechaduino is only useful in the context of a larger hardware/software ecosystem. For example, there might be a program running on a laptop that communicates with the Mechaduino using a serial protocol. Would such a program also need to be released under the same license?

3. The CC-by-SA license is incompatible with other software licenses. Does that mean I wouldn't be able to use any libraries licensed under different terms in conjunction with Mechaduino?

4. If I use the Mechaduino, I would like to share the improvements I make. In particular, I would implement #25, substantially improve the PID tuning experience, and possibly implement #19. For PID tuning, I would create a program that graphs `yw` and `r` and allows users to adjust P,I,and D while the motor is following a square wave. Would I need to release that program under the same CC-by-SA license?

5. If I implement #25, I would like to improve the documentation pdf and release the new pdf under CC-by-SA v4. Could I get access to the source files used to make that pdf, for that purpose?

Thanks in advance!

jcchurch13, 2018-04-07:
The intent of this license is to keep any derivatives of the Mechaduino Hardware/Firmware open source.  The CC-BY-SA license seems to capture this intent better than any other license I am familiar with, but it is not perfect.  I'll try to advise on your specific concerns, but these are just answers off the top of my head.  (I haven't spent too much time considering every possible scenario.  The answers below do not supersede the actual license, they're just my best guess at interpreting it).  I haven't consulted our legal team on this, and I hope not to need to ;)
In general, please just use your best judgement.

1)No need to share minor parameter changes.  If you add some functionality that someone else might find useful, please share it.

2)If you develop something specifically to interface with the Mechaduino, please share it.

3)If you want to use the Mechaduino with an existing library that uses a different license/is closed source, that seems fine to me.  If you develop a library specifically to use with the Mechaduino, but you put a more restrictive license on it, that would not be cool.

4)  Awesome!  If you were to develop software tools for the Mechaduino, yes, please release them as open source.  I'm not sure if this falls under the scope of the CC-BY-SA share alike requirement, but I personally wouldn't have a problem with you releasing any original code you develop for tuning the Mechaduino under a less restrictive license like the MIT license.

5)  Awesome!  We are about to release a long over-due update to the manual.  When we release this, I'll release the source files to the pdf so that others can modify.

Thanks for asking!
-Joe

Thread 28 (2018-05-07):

Calibration Settings

yngndrw, 2018-05-07:
This is a really cool project that I'm very interested in, but one thing that stood out to me was the need for recompilation when changing settings and during calibration.

Now I'm aware that this microcontroller doesn't have any EEPROM storage, but there are some libraries to use the flash memory for this purpose. https://github.com/cmaglie/FlashStorage

By using flash storage for the calibration, it would then be possible to have the calibration routine writes its calibration directly and skip the recompilation step, making Mechaduino much easier to use.

osresearch, 2018-06-09:
PR #30 adds this functionality

Closed 2020-10-09.

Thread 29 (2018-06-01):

PIn mappings for step/dir?

osresearch, 2018-06-01:
Which pins are supposed to be used for step and direction?  I see in `#define step_pin 1` definition in https://github.com/jcchurch13/Mechaduino-Firmware/blob/master/Mechaduino/Mechaduino/Parameters.h#L59 and the schematic looks like it should have external pullups on it, but pulsing pin D1 to ground doesn't seem to make it step in position hold mode or in open-loop mode.

Enabling the control loop with `y` and using `r` to set the set points works, so am I missing something or does a different mode need to be enabled?

osresearch, 2018-06-01:
Ah, I found it -- yes, the `configureStepDir()` function needs to be called to enable the step and direction input pins (D1 and D0): https://github.com/jcchurch13/Mechaduino-Firmware/blob/master/Mechaduino/Mechaduino/Mechaduino.ino#L71

Closed 2018-06-01.

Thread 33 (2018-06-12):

Ramp up effort when enabling closed loop

osresearch, 2018-06-12:
The motor command goes to 100% as soon as the closed loop is enabled, leading to a sharp jolt.  It would be nice to have to effort ramp up so that it doesn't shock load the system.

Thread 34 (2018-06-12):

Hall sensors are dry all over the planet

udidnazime, 2018-06-12:
The AS5047D hall sensors are dry all over the planet, are there any alternatives that can be used for your project? Or do you know where one can still find them?

wjsteele, 2019-01-17:
Mouser and Digikey both show plenty of stock. (This is as of 16 January 2019)

Closed 2020-10-09.

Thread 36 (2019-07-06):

Only three different step phases in a four phase step sequence? - two are duplicate

tarchive, 2019-07-06:
Hello,

I am sure that i am missing something here but why are there only 3 different phases when stepping the motor?

Since i am still doing some initial testing, i am current running this on my Arduino Zero.
I discovered when probing pins 5, 6 ,7 ,8 and manually commanding steps from serial console, i would see the following pattern:
(Excuse my crude table)

                D8      D7       D5      D6
               IN_1    IN_2     IN_3    IN_4
    Phase 1:    L       H        L       H
    Phase 2:    L       H        H       L
    Phase 3:    H       L        L       H
    Phase 4:    L       H        L       H

As you can see, phase 1 and 4 are the same. I would have expected to see H L H L in one of them instead. Digging, I think i found the responsible code in the utils.cpp and the way it was written makes this seem intentional.

So either i am having a brain fart today or something is going on here.

Thanks

Quas7, 2019-11-10:
Hi,

quite old issue but did you have a look into the A4954 pwm motor driver datasheet? http://elecanisms.olin.edu/handouts/2.3_A4954-Datasheet.pdf

Your fining might be related to the chopping mode.

tarchive, 2019-11-20:
Thanks for the reply Quas7
You are make me rethink this again because i did not test the pins with my oscilloscope to see the PWM duty though i don't think that's the issue.
In my test i was using an Arduino Zero and LEDS on the output digital IO step pins labeled above. No A4954 driver was used so i did not actually test the drivers output either. However, i don't think this matters because the driver is just two full bridge drivers that relies on 4 IN signals to sequence the steps. The PWM is for decay control and does not affect the step sequence. In the table on page 4 it only shows IN3 and IN4 because its a truth table of a DC motor. Here in this project for one bipolar stepper we need IN1 IN2 IN3 and IN4 so that truth table only illustrates half the picture of whats going on.

Because i am observing this three phase pattern directly from the micro controller, I was thinking there is something seriously wrong with my setup. Though i was using vanilla code directly from the master branch. The really concerning part for me is that by manually telling the micro controller to step through the phases, i can see it pause where there is a duplicate phase. The micro controller knows there are 4 phases, its just duplicating one for some reason.

Since this post, i have already disassembled my test board and went with another Coretex-M0 compatible closed loop stepper driver project that has worked..alright for me.

I would still love to get to the bottom of this so i do appreciate all comments or explanations no matter how long since the original post. Thank you.

Varghesemela, 2020-10-09:
I am facing the same issue,
i uncommented the "debugging phase voltage" snippet at Line 112 in Utils.cpp. The serial monitor readings for the v_coil_A and v_coil_B are as below for single step sequence:
 0,    37
37,    0
 0,   -37
-37,   0
And i also managed to get the output readings per hase for every 4 sequence which is as below:
0110
0101
1010
0110
As i can see one sequence gets repeated which is similar to this issue raised. Please let me know if anyone has an explanation.

Quas7, 2020-10-09:
There is some additional explanation, how this works for the Mechkaduino re-works on STM32 basis here: https://github.com/makerbase-mks/MKS-SERVO42B/issues/8
Maybe this helps.

jcchurch13, 2020-10-09:
Let me see if I can clarify what is happening here:
IN_1 and IN_2 set the direction and decay mode for Phase A, and IN_3 and IN_4 set the direction and decay mode for Phase B.  (H,L) is forward and (L,H) is reverse.  However, the phase current is set by the V_REF pins on the A4954.

The logic in the firmware is to set the direction pins as follows:

`  v_coil_A = ((effort * sin_coil_A) / 1024);
  v_coil_B = ((effort * sin_coil_B) / 1024);

  analogFastWrite(VREF_1, abs(v_coil_A));
  analogFastWrite(VREF_2, abs(v_coil_B));

  if (v_coil_A >= 0)  {
    IN_2_HIGH();  //REG_PORT_OUTSET0 = PORT_PA21;     //write IN_2 HIGH
    IN_1_LOW();   //REG_PORT_OUTCLR0 = PORT_PA06;     //write IN_1 LOW
  }
  else  {
    IN_2_LOW();   //REG_PORT_OUTCLR0 = PORT_PA21;     //write IN_2 LOW
    IN_1_HIGH();  //REG_PORT_OUTSET0 = PORT_PA06;     //write IN_1 HIGH
  }

  if (v_coil_B >= 0)  {
    IN_4_HIGH();  //REG_PORT_OUTSET0 = PORT_PA20;     //write IN_4 HIGH
    IN_3_LOW();   //REG_PORT_OUTCLR0 = PORT_PA15;     //write IN_3 LOW
  }
  else  {
    IN_4_LOW();     //REG_PORT_OUTCLR0 = PORT_PA20;     //write IN_4 LOW
    IN_3_HIGH();    //REG_PORT_OUTSET0 = PORT_PA15;     //write IN_3 HIGH
  }

}`
When the Mechaduino performs single steps, it turns one phase on at a time in either forward or reverse.

The asymmetry arises due to the case when v_coil_X is 0.  When you are commanding 0 current, it should not really matter whether you are in "forward" (H,L), or "reverse" (L,H), because that phase is effectively off.

This is all handled by the output function in Utils.cpp, which handles sinusoidal commutation of the motor phases.  This is used by both the closed loop modes and open loop stepping.   If this logic were faulty, the closed loop sinusoidal commutation would not work properly.  For open loop stepping excitation angle is just stepped by 90 electrical degrees.  In these cases you get v_coil_X set to exactly 0 on one phase at a time.  The logic above determines the IN_X "direction" by checking if v_coil_X is >= 0.  Based on this logic you get the following step pattern:

v_coil_A, v_coil_B:  37,0
IN_1, 2, 3, 4:  0,1,0,1

v_coil_A, v_coil_B:  0,-37
IN_1, 2, 3, 4:  0,1,1,0

v_coil_A, v_coil_B:  -37,0
IN_1, 2, 3, 4:  1,0,0,1

v_coil_A, v_coil_B:  0,37
IN_1, 2, 3, 4:  0,1,0,1

As a test, I tried adding a small offset to the step angle to avoid the case where v_coil_X = 0.   The results give four distinct IN_X codes, but there is no noticeable difference in operation:

v_coil_A, v_coil_B:  36,-1
IN_1, 2, 3, 4:         0,1,1,0

v_coil_A, v_coil_B:  -1,-36
IN_1, 2, 3, 4:         1,0,1,0

v_coil_A, v_coil_B:    -36,1
IN_1, 2, 3, 4:           1,0,0,1

v_coil_A, v_coil_B:  1,36
IN_1, 2, 3, 4:         0,1,0,1

I agree, it does look odd at first glance, but I don't think there is really an issue here unless someone is seeing unexpected behavior in the phase waveforms.

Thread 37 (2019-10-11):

Geared Motor

mmwolbrink, 2019-10-11:
When using 5x geared stepper motor in closed loop the motor goes into constant rotation at high speed when applying torque on the axle.

Closed 2020-01-15.

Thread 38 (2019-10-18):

Latest code does not compile

AThilenius, 2019-10-18:
Starting with [this commit](https://github.com/jcchurch13/Mechaduino-Firmware/commit/055bc004133c3f7c70fbc5b1394e09163140d0f2) the `FlaggedStorage` library was used, resulting in the compilation error: `FlashStorage.h: No such file or directory` on a clean Arduino install.

Repro steps:
- From a clean Arduino install
- Add `Arduino SAMD Boards (32-bit ARM Cortex-M0+)` in the Board Manager
- Git clone `master`
- Open `Mechaduino\Mechaduino\Mechaduino.ino`
- Select any `Arduino Zero` (doesn't matter, all fail)
- Hit `Verify`

Given that the README says "New firmware is in the default "master" branch" I think it's expected that the master branch be green (would recommend some CI).

Latest `Release` still works.

charles-blouin, 2020-10-05:
Temporary workaround: Sketch>Include Library> Manage Library

Look for the library FlashStorage, and install version 0.7.1

mmwolbrink, 2020-10-06:
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

Thats not a workaround, you are supposed to do that anyway.

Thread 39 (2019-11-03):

How to unbrick a fully bricked Mechaduino (general SAMD21 issue, not firmware related)

Quas7, 2019-11-03:
Just wanted to share my experience with a hard bricked Mechaduino v0.2.

The SAMD21 is known to get his flags/fuses mixed up in some programming situations.
In this case, the bootloader area is set to write-protected and re-flashing the Arduino Zero bootloader via SWD port will fail.

A possible solution, if you do not have an ATMEL-ICE is using a black magic probe (BMP).
https://1bitsquared.de/products/black-magic-probe

Fortunatelly, a "Blue Pill" (STM32 dev board) can be programmed to function as a BMP.
https://buger.dread.cz/category/stm32.html

The solution is coming from here:
https://electronics.stackexchange.com/questions/438386/samd21-how-do-i-write-to-nvm-fuses

*$ /home/peter/snap/arduino-mhall119/5/.arduino15/packages/arduino/tools/arm-none-eabi-gcc/7-2017q4/bin/arm-none-eabi-gdb*

(gdb) target extended-remote /dev/ttyACM0
Remote debugging using /dev/ttyACM0
(gdb) monitor swdp_scan
Available Targets:
No. Att Driver
 1      Atmel SAMD21G18A (rev D) M0+
(gdb) attach 1
Attaching to Remote target
warning: No executable has been specified and target does not support
determining executable automatically.  Try using the "file" command.
0x00001314 in ?? ()
(gdb) file samd21_sam_ba.hex
A program is being debugged already.
Are you sure you want to change the file? (y or n) y
Reading symbols from samd21_sam_ba.hex...(no debugging symbols found)...done.
(gdb) monitor unlock_flash
(gdb) monitor unlock_bootprot
(gdb) monitor erase_mass
Erase successful!
(gdb) load
Loading section .sec1, size 0x1968 lma 0x0
Start address 0x60c, load size 6504
Transfer rate: 37 KB/sec, 929 bytes/write.

Quas7, 2019-11-03:
for information only

Closed 2019-11-03.

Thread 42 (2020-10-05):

unable to compile.

killisch, 2020-10-05:
Unable to compile the firmware with the latest arduino release 1.8.13
unsure what the issue is. fails to verify in multiple locations and I'm not advanced enough to troubleshoot on my own.
currently mechaduino's are paperweights.

Closed 2020-10-05.

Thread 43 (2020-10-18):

Anti-cogging, proof on concept

charles-blouin, 2020-10-18:
Hello there,

I made a test implementation of anticogging. Here is a [video](https://youtu.be/VyuWUg4WjfY). It is especially noticeable for fine control in velocity and torque mode.

The calibration is done in python for now. It should be migrated to the firmware, similarly to the encoder calibration.

The calibration is longer, as it requires finer steps. It should be done if forward and reverse direction, and averaged, as there is a constant friction term. The blue line is a calibration pass in both directions.

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

Changes to mechaduino:
https://github.com/charles-blouin/Mechaduino-Firmware/commits/cogging
Calibration code
https://gitlab.com/charles-blouin/pendulum-ml/-/tree/master/anticogging_calibration

 You can run 'measure-torque-ripple' followed by interpolate_360

ChristianFrisson, 2020-10-26:
Hi @charles-blouin, anti-cogging is a very interesting feature for Mechaduinos and your [video](https://youtu.be/VyuWUg4WjfY) is compelling!

I can access your [github fork](https://github.com/charles-blouin/Mechaduino-Firmware/commits/cogging), but I can not reach your [gitlab repository](https://gitlab.com/charles-blouin/pendulum-ml/) (error 404 Not Found). Could you please check?

Kind regards,
Christian

charles-blouin, 2020-10-26:
@ChristianFrisson Sorry about this, it is fixed.

It may be possible to reuse the rotary encoder calibration code for an anticogging calibration routine. The hardware may have just enough RAM. Right now, the encoder is calibratedwith 200 points in an array named fullStepReadings[spr]. For the anticogging, we need a little over 360*4 points. The calibration could be done in two passes, so the full calibrated array with 16k points would be updated after the second calibration pass.

mmwolbrink, 2021-02-03:
This Sparked my interest, I'm going to see if I can integrate this into mechaduino firmware. I will keep you guys posted.

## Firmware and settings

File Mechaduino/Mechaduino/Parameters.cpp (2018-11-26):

//Contains the Mechaduino parameter defintions

#include <Wire.h>
#include "Parameters.h"
#include "math.h"


//----Current Parameters-----

volatile float Fs = 6500.0;   //Sample frequency in Hz

volatile float pKp = 15.0;      //position mode PID values.  Depending on your motor/load/desired performance, you will need to tune these values.  You can also implement your own control scheme
volatile float pKi = 0.2;
volatile float pKd = 250.0;//1000.0;
volatile float pLPF = 30;       //break frequency in hertz

volatile float vKp = 0.001;       //velocity mode PID values.  Depending on your motor/load/desired performance, you will need to tune these values.  You can also implement your own control scheme
volatile float vKi = 0.001;
volatile float vKd = 0.0;
volatile float vLPF = 100.0;       //break frequency in hertz

// This is the encoder lookup table (created by calibration routine):

const float __attribute__((__aligned__(256))) lookup[16384] = {
//Put lookup table here!
};



volatile float pLPFa = exp(pLPF*-2*3.14159/Fs); // z = e^st pole mapping
volatile float pLPFb = (1.0-pLPFa);
volatile float vLPFa = exp(vLPF*-2*3.14159/Fs); // z = e^st pole mapping
volatile float vLPFb = (1.0-vLPFa)* Fs * 0.16666667;


const int spr = 200;                // 200 steps per revolution  -- for 400 step/rev, you should only need to edit this value
const float aps = 360.0/ spr;       // angle per step
int cpr = 16384;                    // counts per rev
const float stepangle = aps/32.0;   // for step/dir interrupt: aps/32 is the equivalent of 1/32 microsteps

volatile float PA = aps;            // Phase advance...aps = 1.8 for 200 steps per rev, 0.9 for 400

const float iMAX = 1.0;             // Be careful adjusting this.  While the A4954 driver is rated for 2.0 Amp peak currents, it cannot handle these currents continuously.  Depending on how you operate the Mechaduino, you may be able to safely raise this value...please refer to the A4954 datasheet for more info
const float rSense = 0.150;
volatile int uMAX = (255/3.3)*(iMAX*10*rSense);   // 255 for 8-bit pwm, 1023 for 10 bit, must also edit analogFastWrite

// A sine lookup table is faster than using the built in sin() function
// for motor commutation... shifted by 0 degrees (this appears to allow
// for a less noisy cal routine) and multiplied by 1024
// generated by:
//  perl -e 'for my $a (0..3600) {
//       printf "%+6.0f,", sin($a * 3.1415 / 180 / 10.0)*1024;
//       print "\n" if $a % 10 == 9;
//  }'
const int sin_1[] = {
    +0,    +2,    +4,    +5,    +7,    +9,   +11,   +13,   +14,   +16,
   +18,   +20,   +21,   +23,   +25,   +27,   +29,   +30,   +32,   +34,
   +36,   +38,   +39,   +41,   +43,   +45,   +46,   +48,   +50,   +52,
   +54,   +55,   +57,   +59,   +61,   +63,   +64,   +66,   +68,   +70,
   +71,   +73,   +75,   +77,   +79,   +80,   +82,   +84,   +86,   +87,
   +89,   +91,   +93,   +95,   +96,   +98,  +100,  +102,  +103,  +105,
  +107,  +109,  +111,  +112,  +114,  +116,  +118,  +119,  +121,  +123,
  +125,  +127,  +128,  +130,  +132,  +134,  +135,  +137,  +139,  +141,
  +143,  +144,  +146,  +148,  +150,  +151,  +153,  +155,  +157,  +158,
  +160,  +162,  +164,  +165,  +167,  +169,  +171,  +173,  +174,  +176,
  +178,  +180,  +181,  +183,  +185,  +187,  +188,  +190,  +192,  +194,
  +195,  +197,  +199,  +201,  +202,  +204,  +206,  +208,  +209,  +211,
  +213,  +215,  +216,  +218,  +220,  +222,  +223,  +225,  +227,  +229,
  +230,  +232,  +234,  +236,  +237,  +239,  +241,  +243,  +244,  +246,
  +248,  +249,  +251,  +253,  +255,  +256,  +258,  +260,  +262,  +263,
  +265,  +267,  +268,  +270,  +272,  +274,  +275,  +277,  +279,  +281,
  +282,  +284,  +286,  +287,  +289,  +291,  +293,  +294,  +296,  +298,
  +299,  +301,  +303,  +305,  +306,  +308,  +310,  +311,  +313,  +315,
  +316,  +318,  +320,  +322,  +323,  +325,  +327,  +328,  +330,  +332,
  +333,  +335,  +337,  +338,  +340,  +342,  +343,  +345,  +347,  +349,
  +350,  +352,  +354,  +355,  +357,  +359,  +360,  +362,  +364,  +365,
  +367,  +369,  +370,  +372,  +374,  +375,  +377,  +379,  +380,  +382,
  +384,  +385,  +387,  +389,  +390,  +392,  +394,  +395,  +397,  +398,
  +400,  +402,  +403,  +405,  +407,  +408,  +410,  +412,  +413,  +415,
  +416,  +418,  +420,  +421,  +423,  +425,  +426,  +428,  +430,  +431,
  +433,  +434,  +436,  +438,  +439,  +441,  +442,  +444,  +446,  +447,
  +449,  +450,  +452,  +454,  +455,  +457,  +458,  +460,  +462,  +463,
  +465,  +466,  +468,  +470,  +471,  +473,  +474,  +476,  +478,  +479,
  +481,  +482,  +484,  +485,  +487,  +489,  +490,  +492,  +493,  +495,
  +496,  +498,  +500,  +501,  +503,  +504,  +506,  +507,  +509,  +510,
  +512,  +514,  +515,  +517,  +518,  +520,  +521,  +523,  +524,  +526,
  +527,  +529,  +530,  +532,  +533,  +535,  +537,  +538,  +540,  +541,
  +543,  +544,  +546,  +547,  +549,  +550,  +552,  +553,  +555,  +556,
  +558,  +559,  +561,  +562,  +564,  +565,  +567,  +568,  +570,  +571,
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

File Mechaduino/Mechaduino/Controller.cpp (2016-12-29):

//Contains TC5 Controller definition
//The main control loop is executed by the TC5 timer interrupt:

#include <SPI.h>

#include "State.h"
#include "Utils.h"
#include "Parameters.h"


void TC5_Handler() {                // gets called with FPID frequency
  
  static int print_counter = 0;               //this is used by step response

  if (TC5->COUNT16.INTFLAG.bit.OVF == 1) {    // A counter overflow caused the interrupt
     
    TEST1_HIGH();  //digitalWrite(3, HIGH);       //Fast Write to Digital 3 for debugging

    y = lookup[readEncoder()];                    //read encoder and lookup corrected angle in calibration lookup table
   
    if ((y - y_1) < -180.0) wrap_count += 1;      //Check if we've rotated more than a full revolution (have we "wrapped" around from 359 degrees to 0 or ffrom 0 to 359?)
    else if ((y - y_1) > 180.0) wrap_count -= 1;

    yw = (y + (360.0 * wrap_count));              //yw is the wrapped angle (can exceed one revolution)


    if (mode == 'h') {                            //choose control algorithm based on mode
      hybridControl();                            // hybrid control is still under development...
    }
    else {
      switch (mode) {
        case 'x':         // position control                        
            e = (r - yw);
            
            ITerm += (pKi * e);                             //Integral wind up limit
            if (ITerm > 150.0) ITerm = 150.0;
            else if (ITerm < -150.0) ITerm = -150.0;          
           
            DTerm = pLPFa*DTerm -  pLPFb*pKd*(yw-yw_1);
           
            u = (pKp * e) + ITerm + DTerm;
           
           
            break;
            
        case 'v':         // velocity controlr
          v = vLPFa*v +  vLPFb*(yw-yw_1);     //filtered velocity called "DTerm" because it is similar to derivative action in position loop

          e = (r - v);   //error in degrees per rpm (sample frequency in Hz * (60 seconds/min) / (360 degrees/rev) )

          ITerm += (vKi * e);                 //Integral wind up limit
          if (ITerm > 200) ITerm = 200;
          else if (ITerm < -200) ITerm = -200;
        
          u = ((vKp * e) + ITerm - (vKd * (e-e_1)));
          
          //SerialUSB.println(e);
          break;
          
        case 't':         // torque control
          u = 1.0 * r ;
          break;
        default:
          u = 0;
          break;
      }

    y_1 = y;  //copy current value of y to previous value (y_1) for next control cycle before PA angle added

    
    if (u > 0)          //Depending on direction we want to apply torque, add or subtract a phase angle of PA for max effective torque.  PA should be equal to one full step angle: if the excitation angle is the same as the current position, we would not move!  
      {                 //You can experiment with "Phase Advance" by increasing PA when operating at high speeds
      y += PA;          //update phase excitation angle
      if (u > uMAX)     // limit control effort
        u = uMAX;       //saturation limits max current command
      }
    else
      {
      y -= PA;          //update phase excitation angle
      if (u < -uMAX)    // limit control effort
        u = -uMAX;      //saturation limits max current command
      }

      U = abs(u);       //

      if (abs(e) < 0.1) ledPin_HIGH();    // turn on LED if error is less than 0.1
      else ledPin_LOW();                  //digitalWrite(ledPin, LOW);


      output(-y, round(U));    // update phase currents
    }
    
   // e_3 = e_2;    //copy current values to previous values for next control cycle
    e_2 = e_1;    //these past values can be useful for more complex controllers/filters.  Uncomment as necessary    
    e_1 = e;
   // u_3 = u_2;
    u_2 = u_1;
    u_1 = u;
    yw_1 = yw;
    //y_1 = y;
    
    if (print_yw ==  true){       //for step resonse... still under development
      print_counter += 1;  
      if (print_counter >= 5){    // print position every 5th loop (every time is too much data for plotter and may slow down control loop
        SerialUSB.println(int(yw*1024));    //*1024 allows us to print ints instead of floats... may be faster
        print_counter = 0;
      }
    }
    TC5->COUNT16.INTFLAG.bit.OVF = 1;    // writing a one clears the flag ovf flag
    TEST1_LOW();            //for testing the control loop timing

  }


}

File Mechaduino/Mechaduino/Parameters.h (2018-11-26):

//Contains the Mechaduino parameter declarations

#ifndef __PARAMETERS_H__
#define __PARAMETERS_H__

#define firmware_version "0.1.5"    //firmware version
#define identifier "x"              // change this to help keep track of multiple mechaduinos (printed on startup)

//----Current Parameters-----

extern volatile float Ts;
extern volatile float Fs;

extern volatile float pKp;
extern volatile float pKi;
extern volatile float pKd;
extern volatile float pLPF;


extern volatile float vKp;
extern volatile float vKi;
extern volatile float vKd;
extern volatile float vLPF;

extern const float lookup[];


extern volatile float pLPFa;
extern volatile float pLPFb;
extern volatile float vLPFa;
extern volatile float vLPFb;


extern const int spr; //  200 steps per revolution
extern const float aps; // angle per step
extern int cpr; //counts per rev
extern const float stepangle;

extern volatile float PA;  //

extern const float iMAX;
extern const float rSense;
extern volatile int uMAX;


extern const int sin_1[];

//Defines for pins:

#define IN_4  6
#define IN_3  5
#define VREF_2 4
#define VREF_1 9
#define IN_2  7
#define IN_1  8
#define ledPin  13
#define chipSelectPin A2 //output to chip select

#define step_pin 1
#define dir_pin 0
#define enable_pin 2

//for faster digitalWrite:
#define IN_1_HIGH() (REG_PORT_OUTSET0 = PORT_PA06)
#define IN_1_LOW() (REG_PORT_OUTCLR0 = PORT_PA06)
#define IN_2_HIGH() (REG_PORT_OUTSET0 = PORT_PA21)
#define IN_2_LOW() (REG_PORT_OUTCLR0 = PORT_PA21)
#define IN_3_HIGH() (REG_PORT_OUTSET0 = PORT_PA15)
#define IN_3_LOW() (REG_PORT_OUTCLR0 = PORT_PA15)
#define IN_4_HIGH() (REG_PORT_OUTSET0 = PORT_PA20)
#define IN_4_LOW() (REG_PORT_OUTCLR0 = PORT_PA20)
#define ledPin_HIGH() (REG_PORT_OUTSET0 = PORT_PA17)
#define ledPin_LOW() (REG_PORT_OUTCLR0 = PORT_PA17)
#define CHIPSELECT_HIGH() (REG_PORT_OUTSET1 = PORT_PB09)
#define CHIPSELECT_LOW() (REG_PORT_OUTCLR1 = PORT_PB09)

#define ENABLE_PROFILE_IO    // Define to enable profiling I/O pins

#ifdef ENABLE_PROFILE_IO  
  #define TEST1   3

  #define TEST1_HIGH() (REG_PORT_OUTSET0 = PORT_PA09)
  #define TEST1_LOW() (REG_PORT_OUTCLR0 = PORT_PA09)

#else
  #define TEST1_HIGH()
  #define TEST1_LOW() 
#endif



#endif

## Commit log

2016-01-03 copied from Stepper_Servo_Prototype_1
2016-01-26 better command_w
    now command_w finds i_step 0 and correct dir based on positive encoder
    direction
    need to get read of i_step/serostate modifiers in c/z?
    output angles seem to to work off the bat
    may need to get rid of 'c' or 'z' functions
2016-01-29 implemented TC5 interrupt, PID
    TC5 interrupt running at 2.5kHz
    great pid settings, but pid is suspect... pure kp behaves odd
2016-01-30 added arduino pid library style pid
    works ok, but oscillates around 0
2016-01-30 Fixed wrap with yw (ywrapped)
    no zero oscillation with arduino style pid
2016-01-30 velocity mode works...
2016-03-17 added current parameter command
    hit 'q' for paramaeters, also added v mode and cleaned up
2016-03-17 adjusting velocity mode
2016-03-24 copied from Mechaduino 0.0
    baseline
    [Mechaduino01.brd, Mechaduino01.sch]
2016-03-24 Revert "copied from Mechaduino 0.0"
    This reverts commit c7bb6a98085dd24362716008a52ce136a40975a1.
    [Mechaduino01.brd, Mechaduino01.sch]
2016-03-30 dispenser pid constants
2016-03-31 electronic gearing/haptics
    implemented with analog setpoints and two motors:
    M1 position --> M2 setpoint
    M2 position --> M1 setpoint
    It works! Could use some filtering to remove noise, but not bad for
    first attempt!
2016-04-01 i2c interrupt works
    also verified (with example code) that Mechaduino_00 hardware works as
    i2c and master using Wire lib. examples
2016-05-19 added Mechaduino 01
    pretty much the same except A2 is CS for encoder instead of A5
2016-06-19 Revert "moving to seperate files"
    This reverts commit ec257edda9c296e06ba1765797bdf8fc7b968cc0.
    [Mechaduino_01.ino]
2016-06-19 Revert "Moving functions to separate file"
    This reverts commit 0127fb6913699b31a3e6c36ecd3e67030672f844.
    [Mechaduino_01.ino]
2016-07-08 Revert "hmmm..."
    This reverts commit 6299245438a9cfd7f93071a908f60e6bef0253a6.
    [Mechaduino_01.ino]
2016-07-08 Revert "multimode demo"
    This reverts commit 3e72f6857e3aaa392333ee65dc70ab10476183ec.
    [Mechaduino_01.ino]
2016-07-09 moving stuff, bumping from error to error
    [Controller.cpp, Mechaduino_01.ino, Parameters.h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]
2016-07-09 moving functions to util as they spout errors
    [Mechaduino_01.ino, Utils.cpp]
2016-07-09 think i got this multiple definition thing licked. moved pin vars
2016-07-09 moved rest of parameter vars except for lookups, which haven't thrown errors yet
    [Parameters.cpp, Parameters.h]
2016-07-09 moved last state vars. joint COMPILES
2016-08-08 Added better current limiting
2016-09-27 some minor fixes
    pi to more digits, corrected fs dependence in velocity loop
    [Controller.cpp, Mechaduino_01.ino, Parameters.cpp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]
2016-09-27 Fixed minor cal routine bug
    [Parameters.cpp, Utils.cpp]
2016-10-15 Added analogFastWrite command
    The latest arduino zero board files (1.6.7 and up) have a much lower PWM
    frequency than previous versions (732.4Hz , down from 187.5kHz). This
    causes audible hissing when used with the Mechaduino. We added the
    analogFastWrite command to provide 187.5kHz PWM to eliminate this issue.
    [Mechaduino_01.ino, Utils.cpp]
2016-10-20 Fixed capitalization error
    state.h -> State.h
    [Mechaduino_01.ino, Parameters.cpp]
2016-11-18 faster SPI, Digital Write
2016-11-18 changed analogFastWrite resolution to 10 bit
    also fixed spi stuff
    [Controller.cpp, Mechaduino_01.ino, Parameters.cpp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]
2016-11-23 changed PWM to true 10-bit, also fixed aps in onestep
    [Mechaduino_01.ino, Parameters.cpp, Utils.cpp]
2016-11-23 Return to 8 bit pwm...
    10 bit worked, lowers pwm frequency... seemed to be more audible noise
    and not as smooth... may revisit at some point.
    [Parameters.cpp]
2016-11-25 clean up, fixed parameter query
    ...moved declarations between state and parameter files (makes more
    sense now).
    [Controller.cpp, Mechaduino_01.ino, Parameters.cpp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]
2016-11-27 Revert "first commit"
    This reverts commit 0f91d381ae8e9491c20469da15cd81e01dfe70ee.
    [Mechaduino_01.ino]
2016-11-29 Revert "more improvements"
    This reverts commit 2a2d0a18485f85471a3c1eef626906117915eafb.
    [Controller.cpp, Parameters.cpp, Parameters.h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]
2016-11-29 Revert "Revert "more improvements""
    This reverts commit 75b1159b6c60dd774297a2c193a2c027d893a0ea.
    [Controller.cpp, Parameters.cpp, Parameters.h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]
2016-11-29 temporary fix for memory bug
    [Mechaduino_01.ino, Parameters.cpp]
2016-11-29 temporary fix for memory bug
    sineGen seems to overwrite stepNumber... better fix coming soon
    [Mechaduino_01.ino]
2016-11-29 fixed memory issue
    sine table no longer stored in ram. It can now be generated from menu.
    [Mechaduino_01.ino, Parameters.cpp, Parameters.h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]
2016-12-03 changing pin definitions to defines from constants
2016-12-07 fixed fast digital write stuff
    using defines now for readability
    [Parameters.h, Utils.cpp]
2016-12-09 fixed a few things
    [Controller.cpp, Mechaduino_01.ino, Parameters.cpp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]
2016-12-22 fixed velocity loop gains
    [Controller.cpp, Mechaduino_01.ino, Parameters.cpp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]
2017-01-05 fixed velocity mode lpf editing
    [Parameters.cpp, Utils.cpp]
2017-01-05 fixed parameter edit bug
    [Utils.cpp]
2017-05-04 changed version, fixed menu 't' issue
    [Mechaduino.ino, Parameters.h, Utils.cpp]
2017-05-04 actually fixed 't' in menu...
    [Utils.cpp]
2018-06-09 Store calibration lookup table in the flash using the FlashStorage library
2018-06-09 Hold current position when closed loop is engaged.
    This also correctly computes the current angle using the lookup
    table, rather than having an approximation of the encoder value.
    [Utils.cpp]
2018-11-24 Minor edits
    Fixed (mostly) an issue with holding the current position when entering
    closed loop mode. This works unless the shaft has moved through 0
    degrees.
    Also added a "calibration complete" message
    [Mechaduino.ino, Parameters.cpp, Utils.cpp]
2018-11-26 Set phase currents to zero when disabled.
